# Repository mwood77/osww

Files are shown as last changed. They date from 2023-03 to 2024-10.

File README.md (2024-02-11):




<div align="center">  
  <h2>
    OSWW
    <p><i>The Open Source Watch Winder</i></p>
  </h2>
</div>

<div align="center">
  <a href="https://www.youtube.com/watch?v=BJKpY6Zp8BI" target="_blank"><strong>👉 See OSWW & Winderoo in action on youtube 👈</strong></a>
  <br>
  <br>
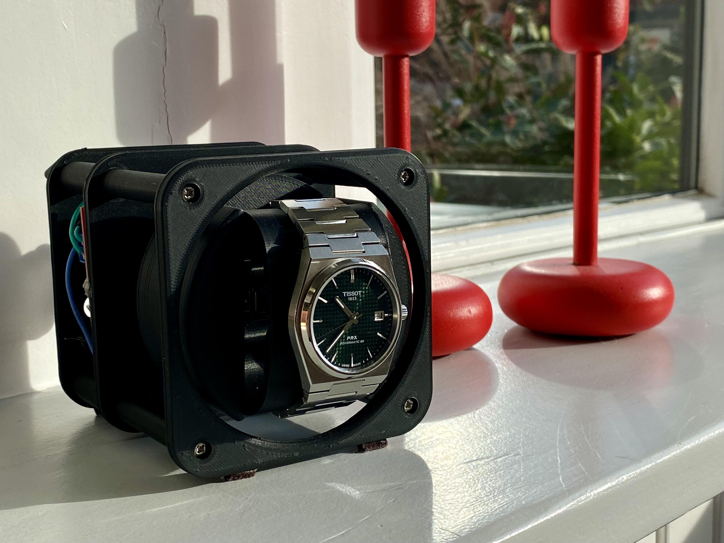
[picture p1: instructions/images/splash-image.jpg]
OSWW - The Open Source Watch Winder
  
  <br>
  <p>
    OSWW is an open source high quality, modular watch winder.
  </p>
</div>

### Key Features
* Silent belt drive
* Minimal electronics / programming experience required
* Easy to print!

## Prerequisites

### Download and install the following:
1. [Arduino IDE](https://www.arduino.cc/en/software)
1. [Add Raspberry Pi Pico to the Arduino IDE](https://www.upesy.com/blogs/tutorials/install-raspberry-pi-pico-on-arduino-ide-software)
   - Do not proceed past the heading "**Upload a program to the Pi Pico**"

## Build Instructions
1. [Bill of Materials (what you need to buy)](./instructions/bom-requirements.md)
1. [Printing Recommendations](./instructions/printing-recommendations.md)
   - [Model Files](./models)
1. [Build Guide](./instructions/build-guide.md)
1. [Wiring Diagram](./instructions/wiring-diagram.md)
1. [Upload the Code](./instructions/upload-code.md)

## Supercharge your OSWW!
> This upgrade requires a different microcontroller
- Checkout [Winderoo](https://github.com/mwood77/winderoo), which adds more complex behaviour and a GUI to your build!

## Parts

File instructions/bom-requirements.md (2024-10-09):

> [👈 Back to main page](../README.md)

# Bill of Materials & Cost

## Tools and skills you already have

- 3D printer + filament (approx 300g per winder)
- Soldering iron & the skills to use it
- Basic tools
    - Screwdriver
    - Hack saw or a rotary tool with a cut-off wheel (to cut the 4mm metal rod to size)
    - Sandpaper or files. This will depend on how dialed-in your 3D printer is.
- Epoxy glue
    - Again, whether you need this or not will depend on how dialed-in your 3D printer is.
- How to use a multimeter (we'll only check for continuity)
- Some spare small-gauge wire (ex. 22 AWG)
- Rudimentary knowledge of electronics

## Required parts
The following parts list will allow you to build:
- 1x powered winder (required)
- 2x un-powered winders (optional)

This means that you'll be able to construct a 3-watch winder. Remember that the system is modular, so if you decide to only build a single powered winder, that's ok.

### Total cost of required Parts
- **$40.00 (February 2023)**

> [!CAUTION]
> If you're planning a [Winderoo](https://github.com/mwood77/winderoo) build, do not purchase a Raspberry Pi Pico. Purchase an ESP32 instead to save some money and avoid future headaches. You can find a link to purchase an ESP32 in [Winderoo's Bill of Materials](https://github.com/mwood77/winderoo/blob/main/docs/bom-requirements.md).

| |  Quantity per Order | Link / Part Name |  Comments |  Cost Incl. Shipping |
| :-: | :---: | :---: | :---: |:-----:|
| 🔲 | 1 | [Raspberry Pi Pico](https://www.raspberrypi.com/products/raspberry-pi-pico/) | Wireless: **NO** & GPIO Headers: **NO** | $5.00 |
| 🔲 | 1 | [608ZZ bearing pack](https://nl.aliexpress.com/item/1005005321486587.html) | 10 bearings per pack | $6.00 |
| 🔲 | 1 | [Electric Motor with gear reduction](https://www.aliexpress.com/item/32987942205.html) | Select: "40 TPM" & "6V". If this is unavailable, buy a `JGA25-370` motor package with planetary gear reduction to run at 35RPM & 5V | $6.00 |
| 🔲 | 1 | [L298N Driver Board](https://nl.aliexpress.com/item/32392774289.html) | Single unit | $3.15 |
| 🔲 | 1 | [Generic Casette Belts](https://www.aliexpress.com/item/4000121675975.html) | Note - you may be able to get away with regular elastic bands, but these will long outlast elastic bands | $2.50 |
| 🔲 | 1 | [M3x20mm Screws](https://aliexpress.com/item/1005005483315023.html) | Select: "M3 50pcs" & "Length 20mm" | $4.00 |
| 🔲 | 1 | [M3 Heat Set Nuts](https://aliexpress.com/item/1005003582355741.html?) | Select: "M3(OD 5mm)" & "Length 5mm 50pcs" | $3.50 |
| 🔲 | 2 | [4mm Steel Rod](https://aliexpress.com/item/1005003594895025.html) | Select: "Diameter 4mm, length 200mm" | $3.75 |

## Optional parts
The following parts list will allow you to add:
- 1x clutch assembly
- 1x physical power button

### Total cost of optional Parts
> $10.60 (February 2023)

| |  Quantity per Order | Link / Part Name |  Comments |  Cost Incl. Shipping |
| :-: | :---: | :---: | :---: |:-----:
| 🔲  | 1 | [Steel Spring](https://aliexpress.com/item/1005002799003214.html) | Select: "25mm Length" & "Wire Diameter 0.4mm" & "Outer Diameter 10mm" | $2.60 |
| 🔲  | 1 | [Felt](https://aliexpress.com/item/1005006650225465.html) | Select: "25CMx85CM" & any colour you choose | $1.50 |
| 🔲  | 1 | [Rocker Switch](https://aliexpress.com/item/4000847897284.html) |  Select: any colour you wish & "Type1 12V LED" & "Wire Diameter 0.4mm" & "21x15mm 3Pin" | $2.10 |

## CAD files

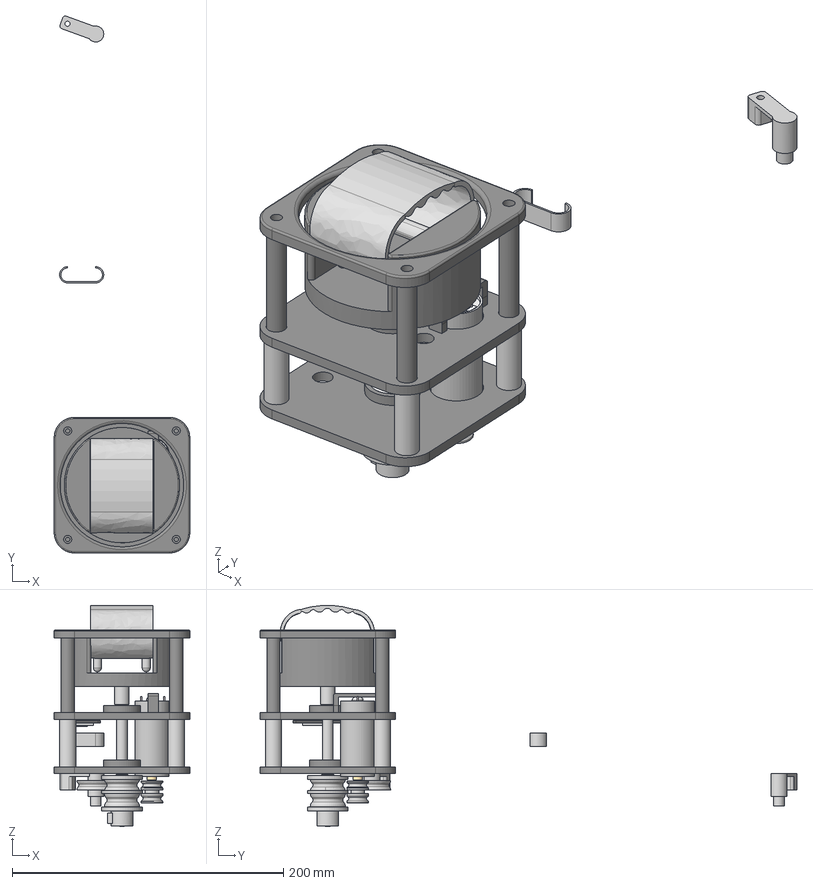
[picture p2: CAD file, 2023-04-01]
models/source-files/osww-v39-april-1-2023.step
100.0 x 395.7 x 162.9 mm
STRUCT-Back Plate-v2
STRUCT-Mid Plate-v2
STRUCT-Front Plate-v2
Brass 4mm diameter rod
Bearings x 3
Inner Race x 3
Outer Race x 3
drive dowel
brass collar
Motor Drive Pulley-v3
M4 Nylon Washer
ESP32-CPU
ESP32-PCB
ESP32-USB_PORT
Tensioner Mount_v2
Tension Pulley_v1
Horizontal Multi Clip
Watch_jig_collar-v4
Watch_Jig_driveshaft-v3
Watch_Jig-v4
Mounting_Dowel_v3 x 4
Mounting_Dowel Sleeve-v3 x 4
Watch Mount-v7
Clutchless-drive_v2
High-Mount_Drive Belt-Tensioner-v1

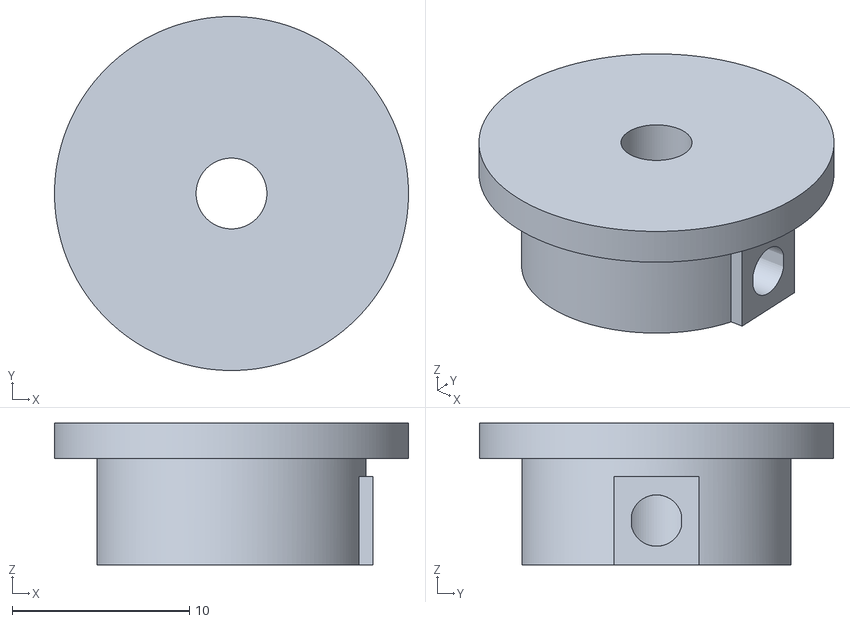
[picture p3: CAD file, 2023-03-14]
models/top_hat_v2.stl
20.0 x 20.0 x 8.00

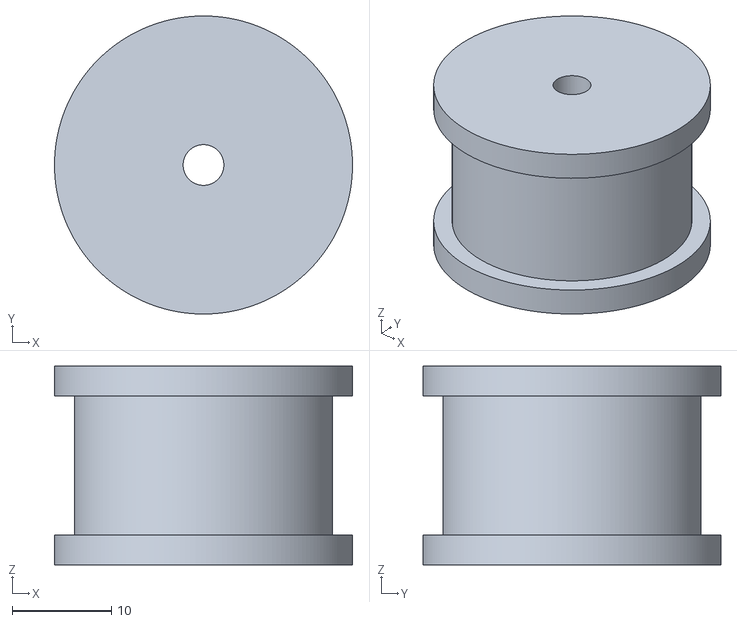
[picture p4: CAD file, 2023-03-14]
models/spring_holder_v3.stl
30.0 x 30.0 x 20.0

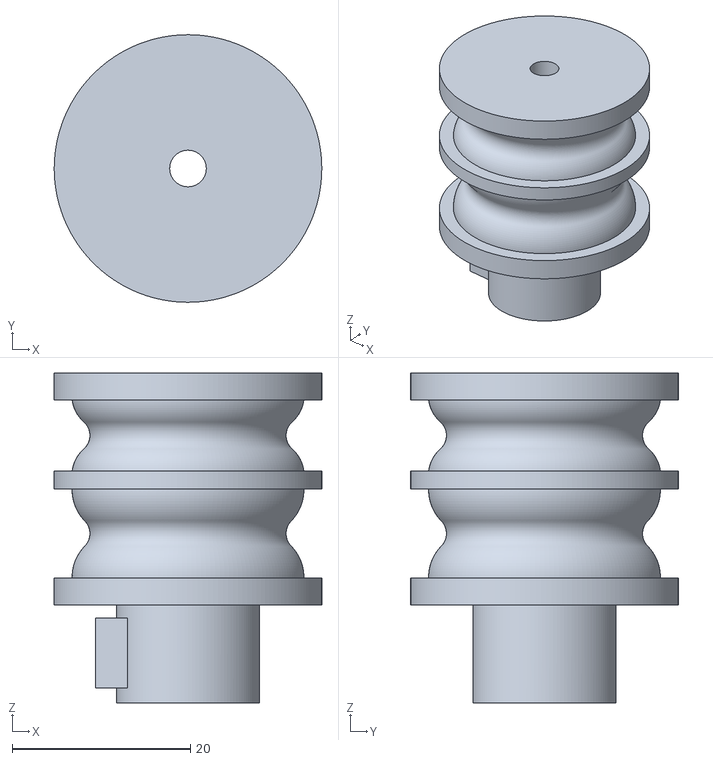
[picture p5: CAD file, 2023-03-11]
models/clutchless_drive_pulley_v2.stl
30.0 x 30.0 x 37.0

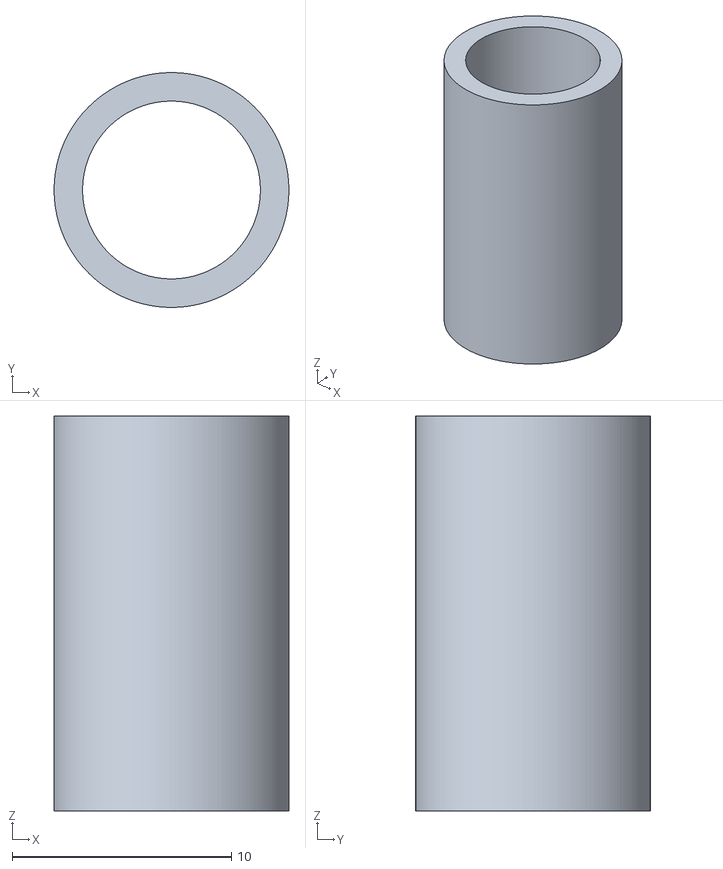
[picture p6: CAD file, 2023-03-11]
models/watch_jig_collar_v4.stl
10.7 x 10.7 x 18.0

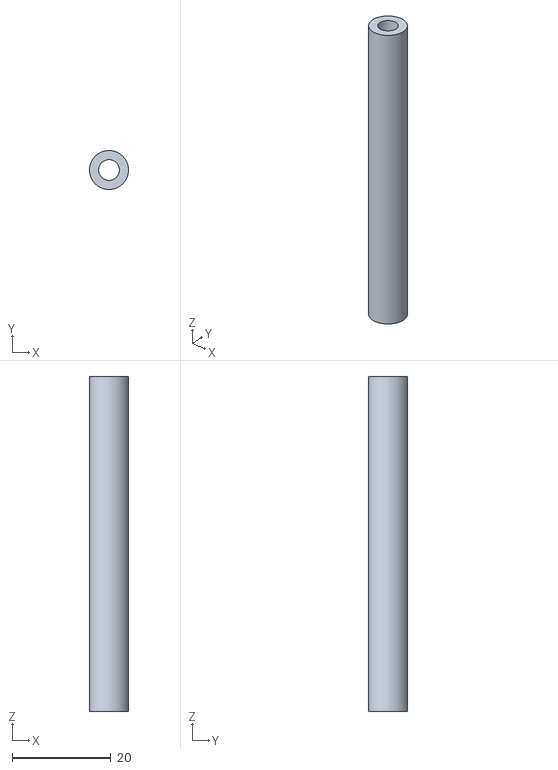
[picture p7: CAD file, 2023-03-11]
models/watch_jig_driveshaft_v3.stl
7.92 x 7.92 x 68.0

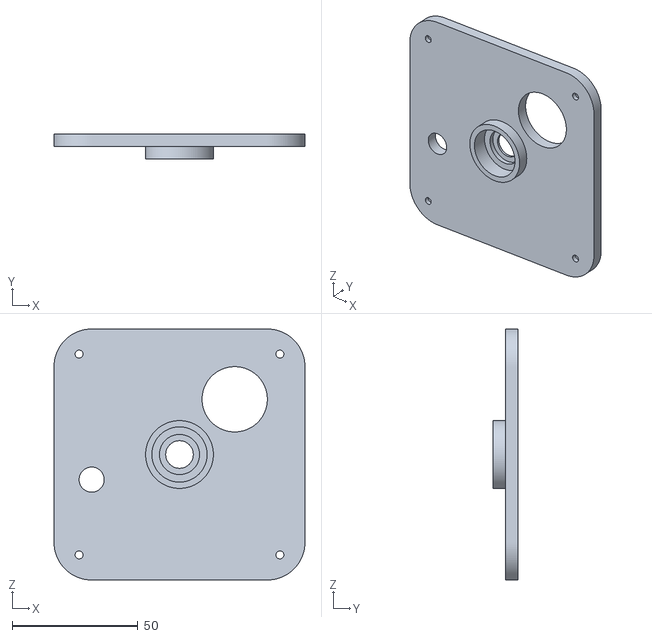
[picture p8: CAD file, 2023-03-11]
models/STRUCT_back_plate_v2.stl
100.0 x 10.0 x 100.0

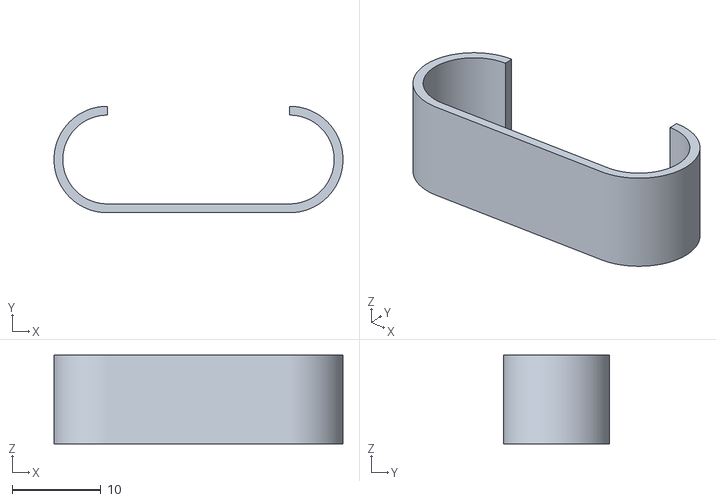
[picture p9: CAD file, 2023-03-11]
models/multi_clip.stl
32.6 x 12.0 x 10.0

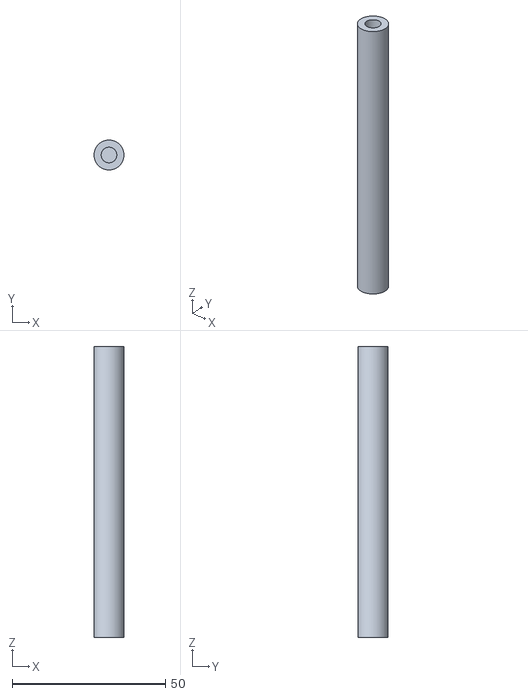
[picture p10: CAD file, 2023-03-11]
models/mounting_dowel_v3.stl
9.80 x 9.80 x 95.0

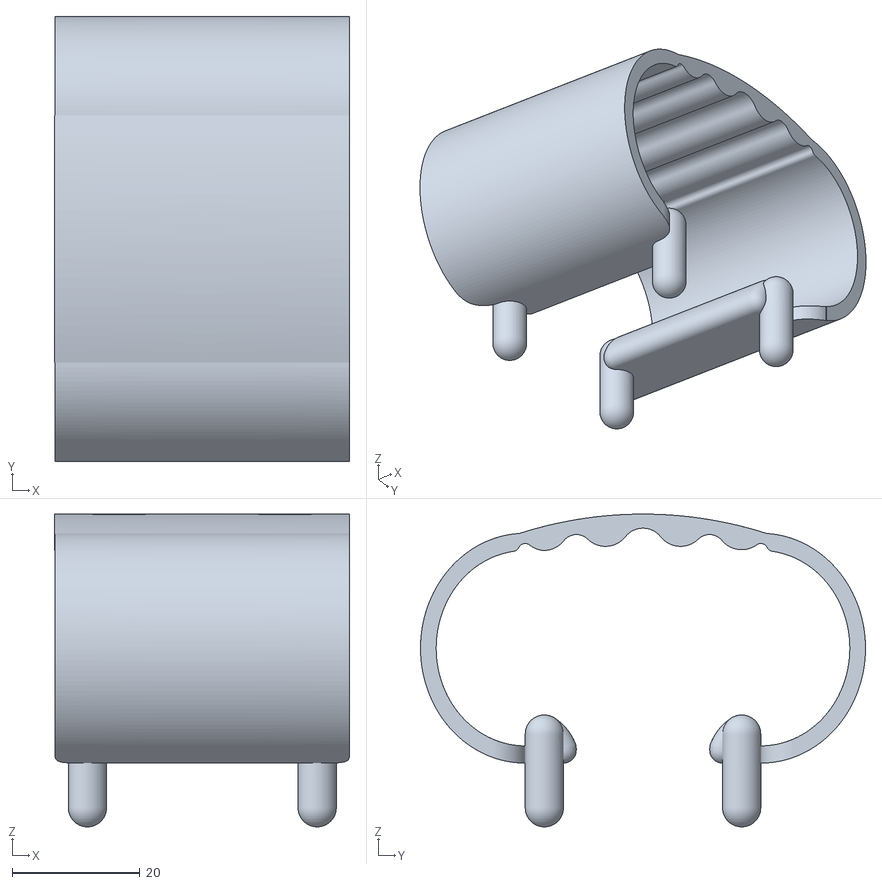
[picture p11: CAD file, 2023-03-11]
models/watch_mount_v7.stl
46.3 x 69.7 x 49.0

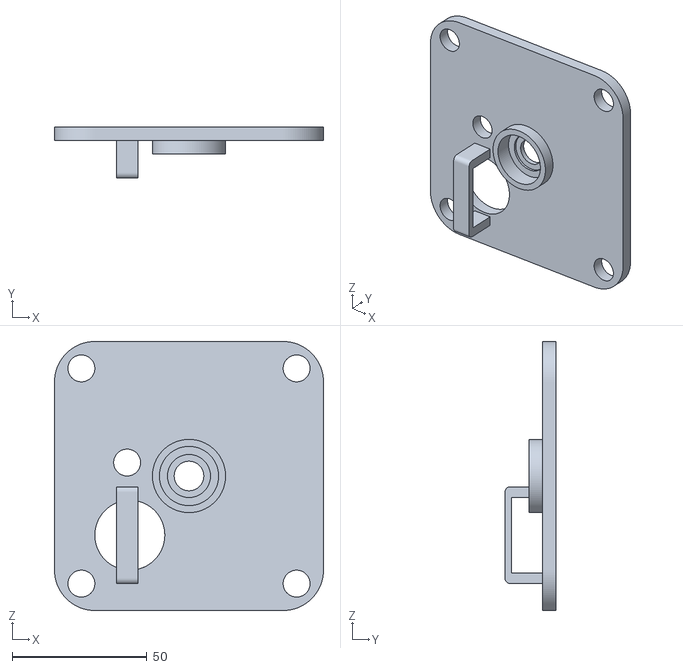
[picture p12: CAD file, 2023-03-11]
models/STRUCT_mid_plate_v2.stl
100.0 x 19.0 x 100.0

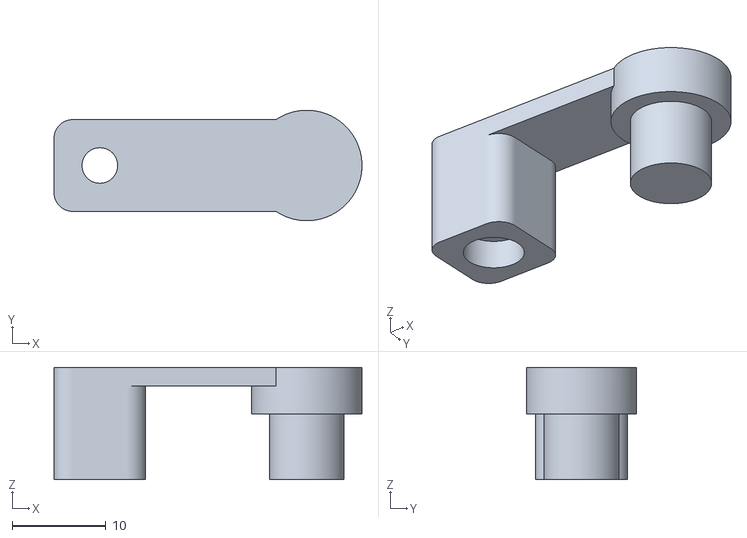
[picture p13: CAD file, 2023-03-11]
models/tensioner_pulley_mount_v2.stl
32.9 x 11.8 x 12.0

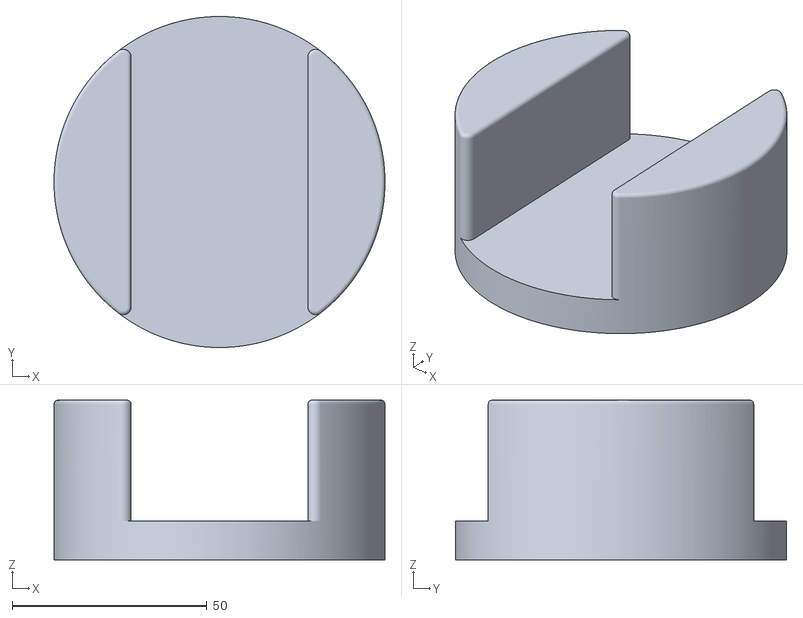
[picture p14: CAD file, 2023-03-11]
models/watch_jig_v4.stl
85.0 x 85.0 x 41.0

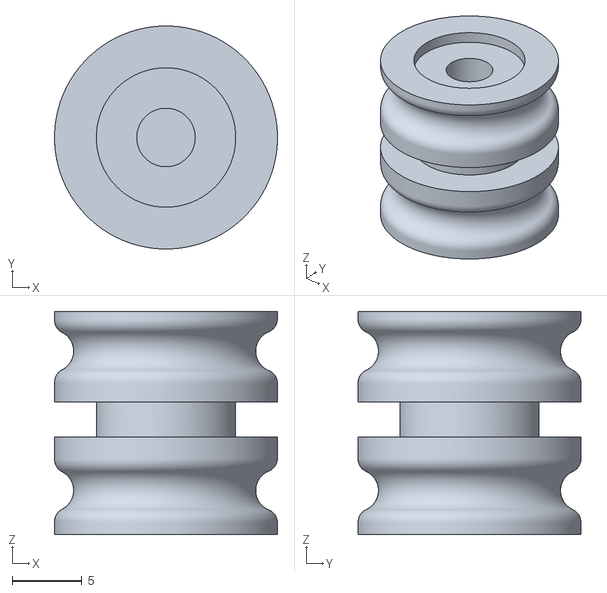
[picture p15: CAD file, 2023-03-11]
models/motor_drive_pulley_v3.stl
16.0 x 16.0 x 16.0

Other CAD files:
models/STRUCT_front_plate_v2.stl
models/high_position_tensioner_pulley_mount_v1.stl
models/tensioner_pulley_v1.stl
models/mounting_dowel_sleeve_v3.stl
models/source-files/osww-v39-april-1-2023.f3d

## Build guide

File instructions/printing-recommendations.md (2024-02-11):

> [👈 Back to main page](../README.md)

# Printing Recommendations
> [!NOTE]
> Total time spent printing is 24 hours per winding unit
>
> Total filament used is approximately 300g per winder

* These are general priting recommendations. 
* Remember that you know your printer better than I.

## General Advice
1. The following models will require support:
    * `STRUCT_mid_plate`
    * `watch_mount`
1. The model is designed to be printed with PLA, therefore tolerances are spec'd for that
    * Tolerances are between `0.1 - 0.2mm`
1. Print with 25% infill
    * This will the increase overall rigidity of the model, especially when dealing with the motor's torque.
    * This will also give you a "premium feeling" product.
1. [If your printer has a tendency elephant foot](https://3dprinterly.com/how-to-fix-bottom-of-3d-print-that-looks-bad/), you'll need to file down some of the pieces.
    * For example, the `mounting_dowel`'s outter lip will need to be filed down so the `mounting_dowel_sleeve` can easily slip over it.

## Recommended Printing Orientation and Print Duration by Model

| Model Name | Quantity To Print | Printing Time Per Unit | Printing Orientation |
| :---: | :---: | :---: | :---:|
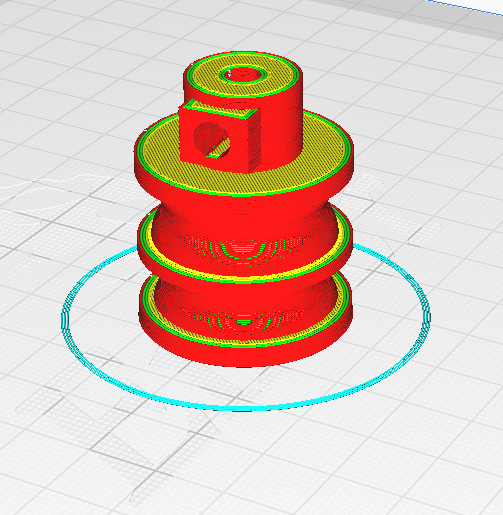
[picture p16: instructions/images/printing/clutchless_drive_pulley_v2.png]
drive_pulley
| `clutchless_drive_pulley_v2` | 1 | 2 hours |  |
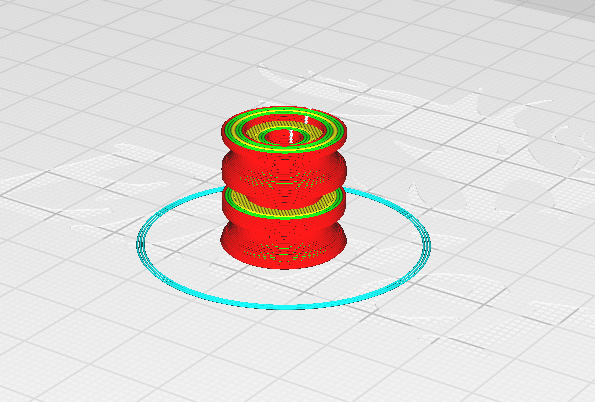
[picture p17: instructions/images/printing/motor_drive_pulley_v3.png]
motor_drive_pulley
| `motor_drive_pulley_v3` | 1 | 0.5 hours |  |
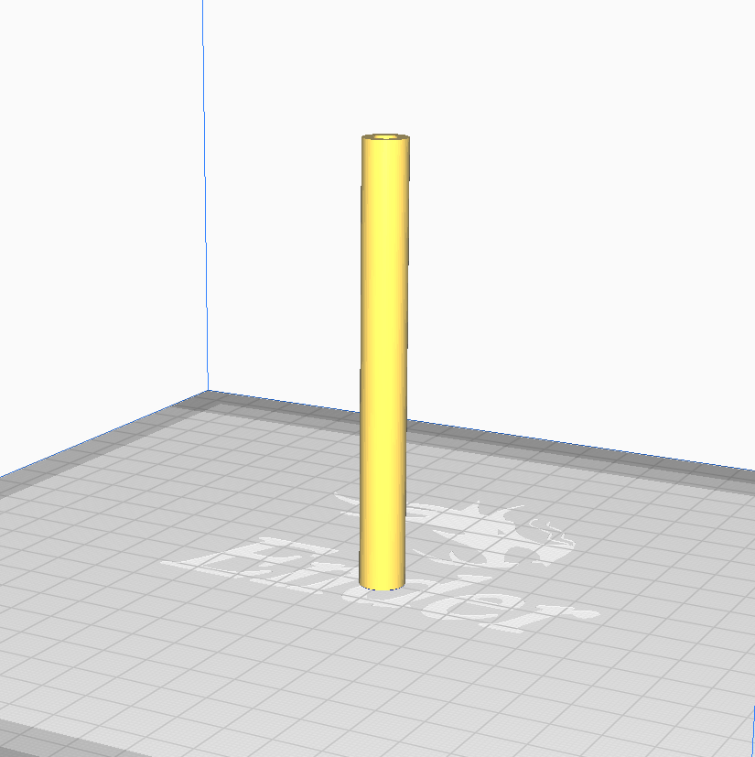
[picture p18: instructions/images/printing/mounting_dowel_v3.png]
mounting_dowel
| `mounting_dowel_v3` | 4 | 0.75 hours p/unit |  |
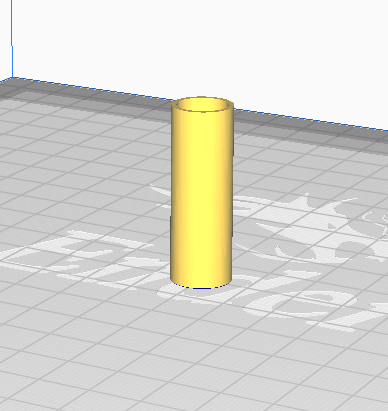
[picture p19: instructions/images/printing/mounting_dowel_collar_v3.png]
mounting_dowel_sleeve
| `mounting_dowel_sleeve_v3` | 4 | 0.25 hours p/unit |  |
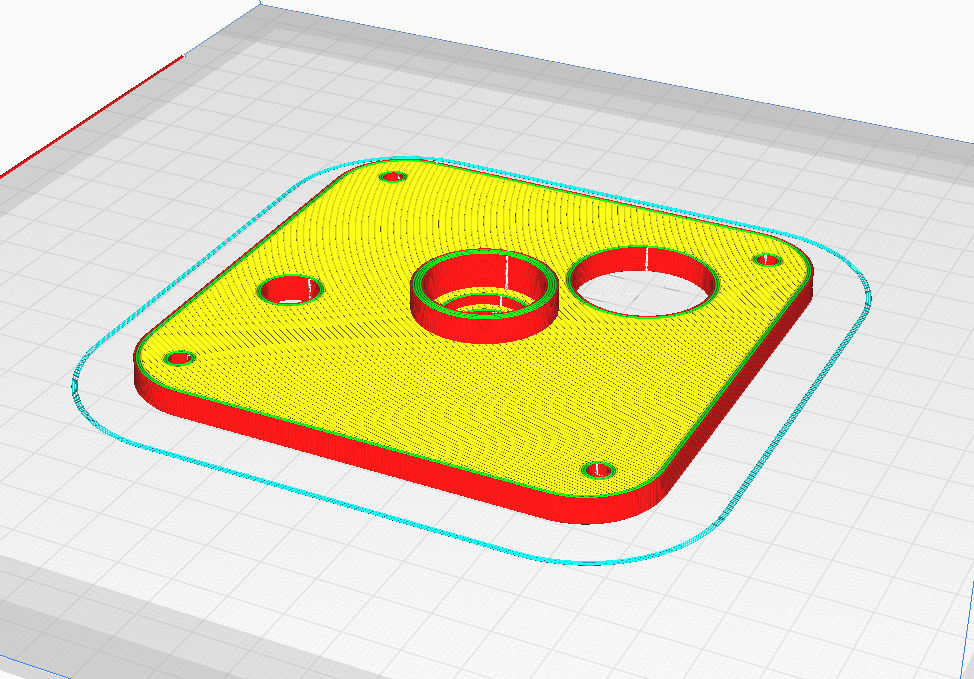
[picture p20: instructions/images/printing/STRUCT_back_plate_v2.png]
STRUCT_back_plate
| `STRUCT_back_plate_v2` | 1 | 3 hours |  |
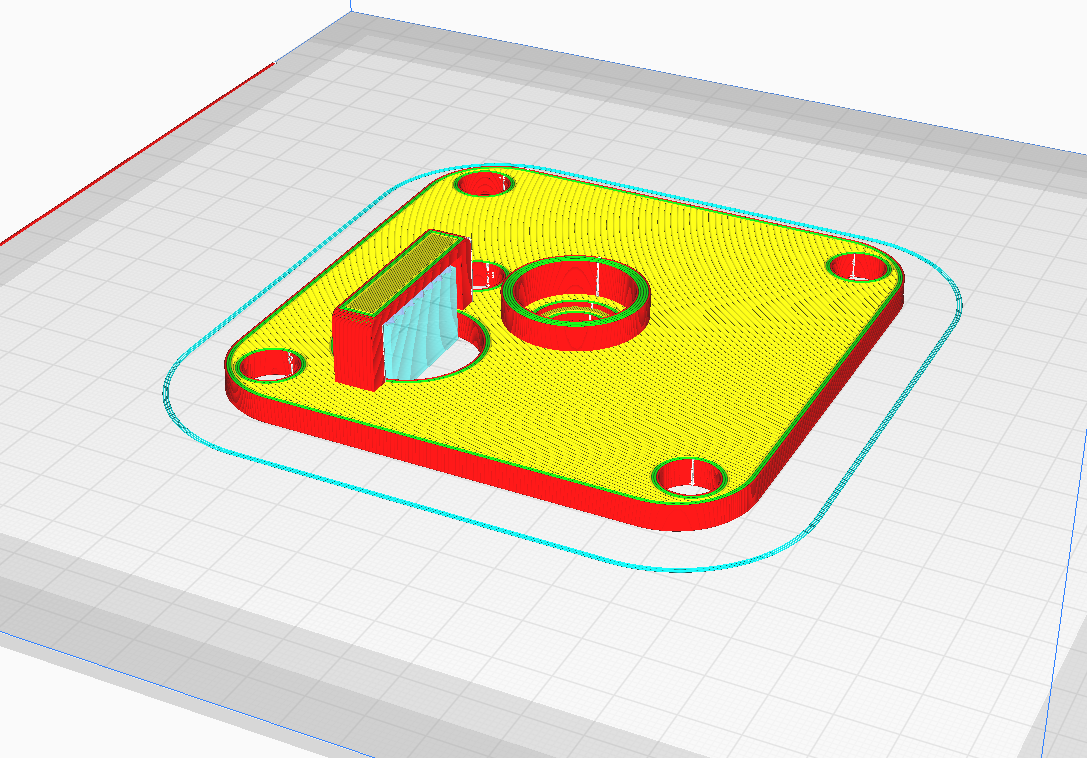
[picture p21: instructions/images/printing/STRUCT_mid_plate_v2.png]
STRUCT_mid_plate
| `STRUCT_mid_plate_v2` | 1 | 3 hours |  |
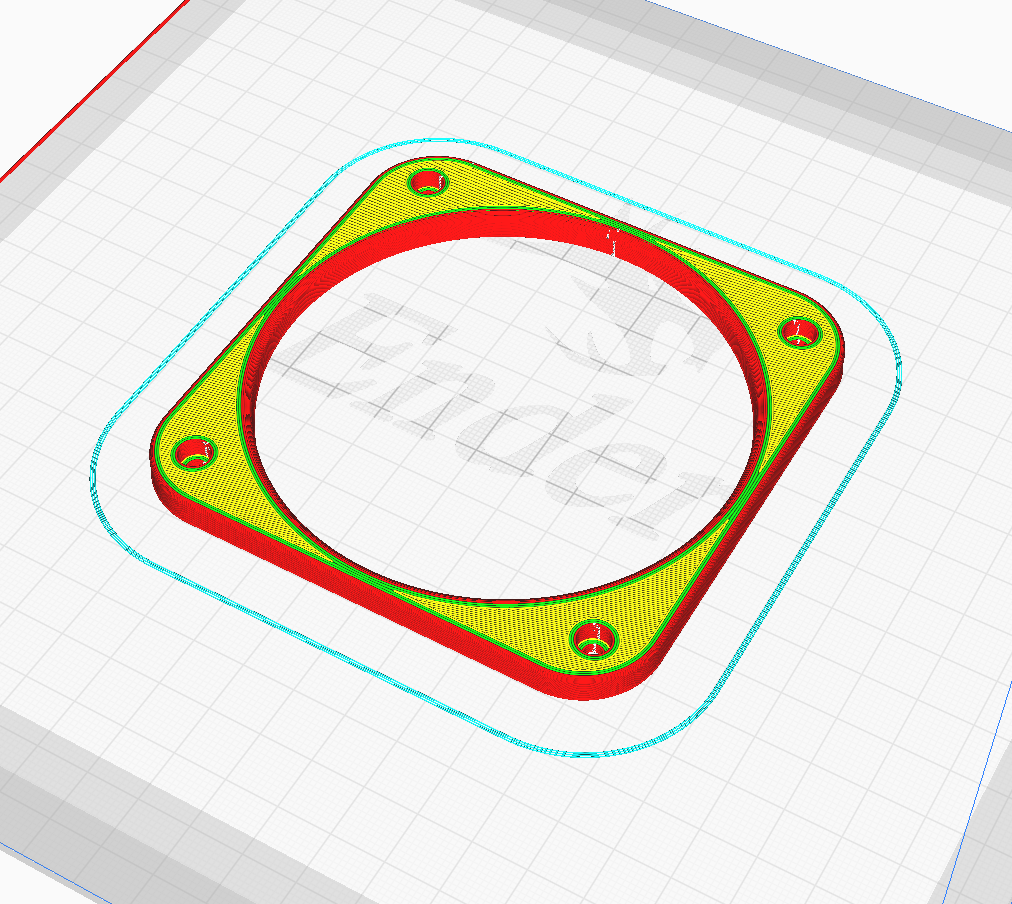
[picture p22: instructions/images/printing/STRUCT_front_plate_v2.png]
STRUCT_front_plate
| `STRUCT_front_plate_v2` | 1 | 2 hours |  |
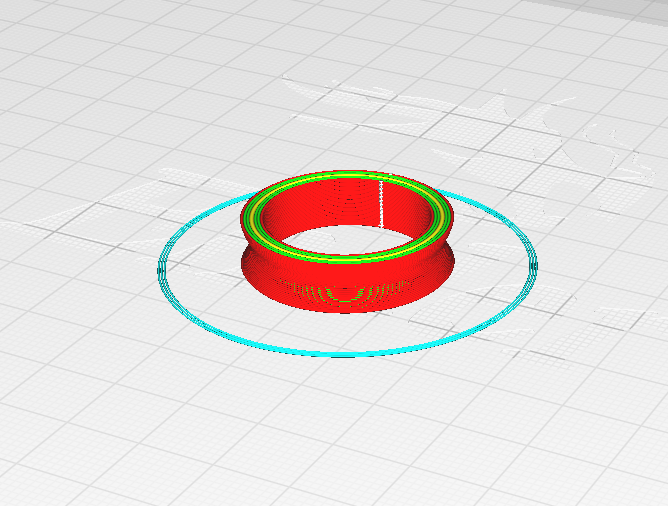
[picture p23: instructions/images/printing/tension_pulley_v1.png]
tensioner_pulley_mount
| `tensioner_pulley_v1` | 1 | 0.25 hours |  |
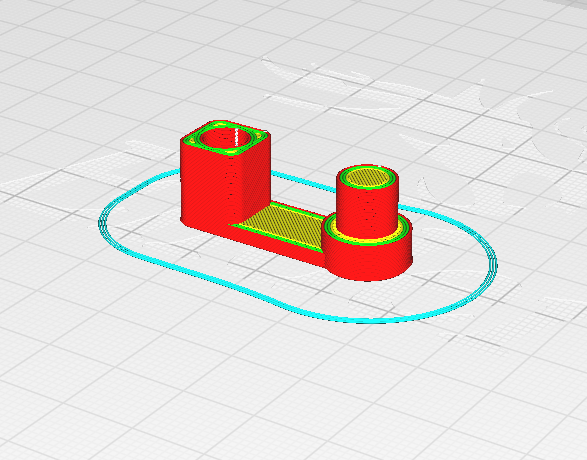
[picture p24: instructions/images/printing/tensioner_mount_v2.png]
tensioner_mount
| `tensioner_pulley_mount_v2` | 1 | 0.25 hours |  |
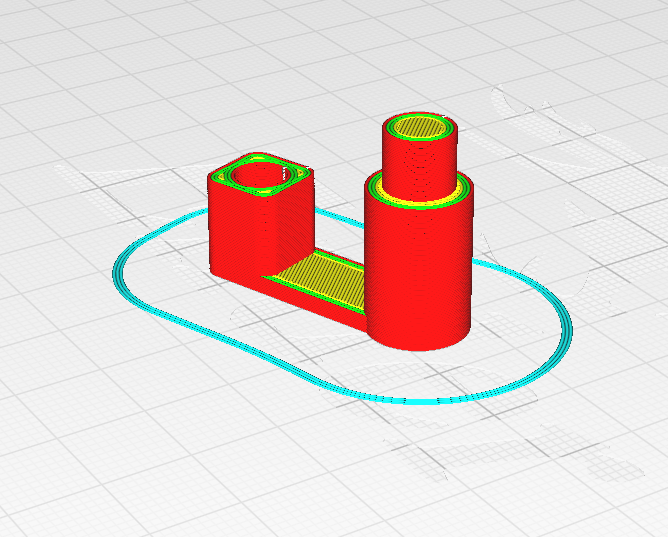
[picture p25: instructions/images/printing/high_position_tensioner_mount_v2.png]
high_position_tensioner_mount
| `high_position_tensioner_pulley_mount_v1` | 1 | 0.25 hours |  |
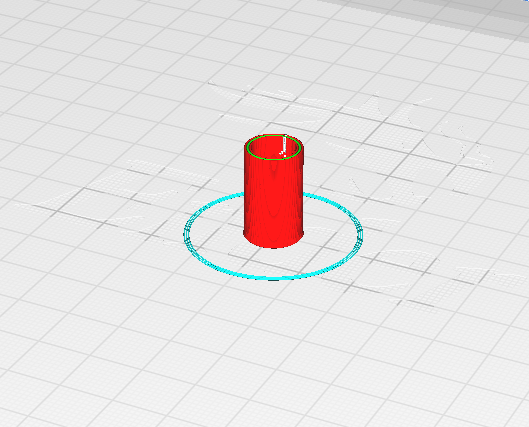
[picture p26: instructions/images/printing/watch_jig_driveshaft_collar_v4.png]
watch_jig_collar
| `watch_jig_collar_v4` | 1 | 0.25 hours |  |
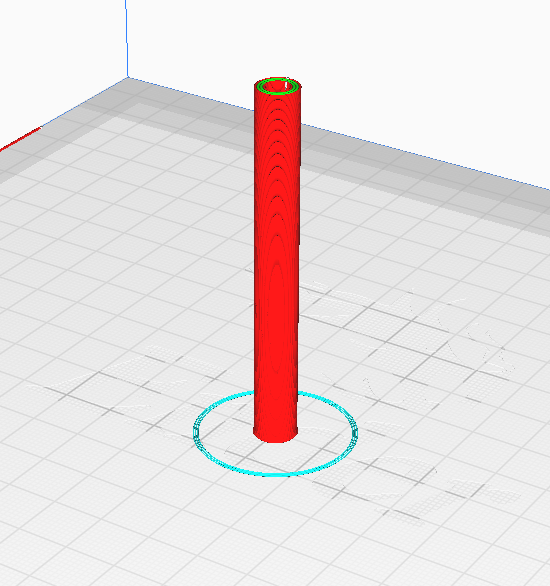
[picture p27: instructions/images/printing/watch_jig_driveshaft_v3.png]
watch_jig_driveshaft
| `watch_jig_driveshaft_v3` | 1 | 1 hour |  |
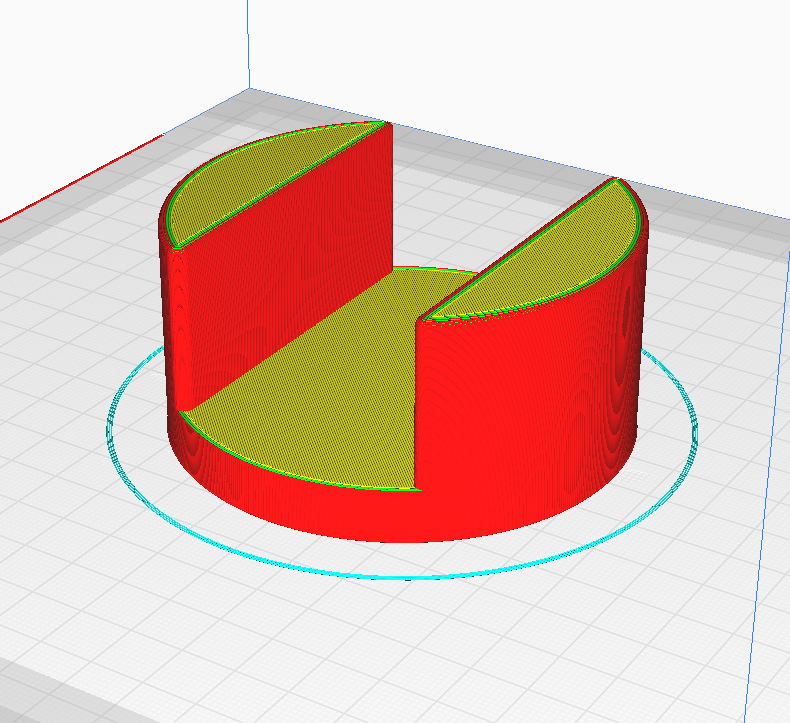
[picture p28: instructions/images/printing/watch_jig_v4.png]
watch_jig
| `watch_jig_v4` | 1 | 6 hours |  |
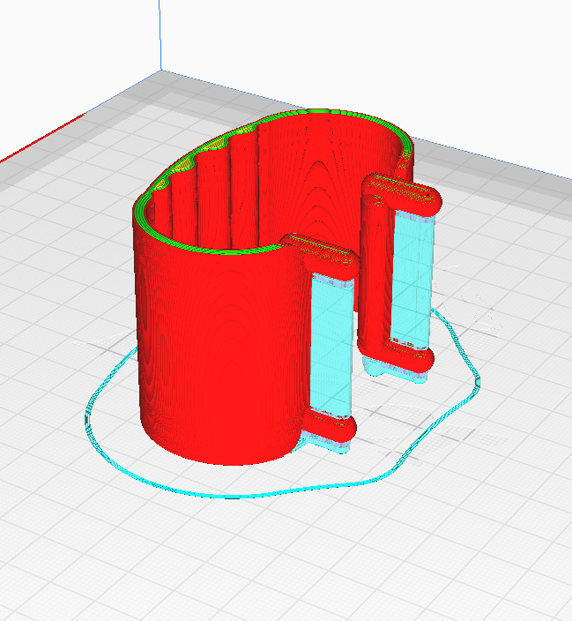
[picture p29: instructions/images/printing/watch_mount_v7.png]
watch_mount
| `watch_mount_v7` | 1 | 2 hours |  |
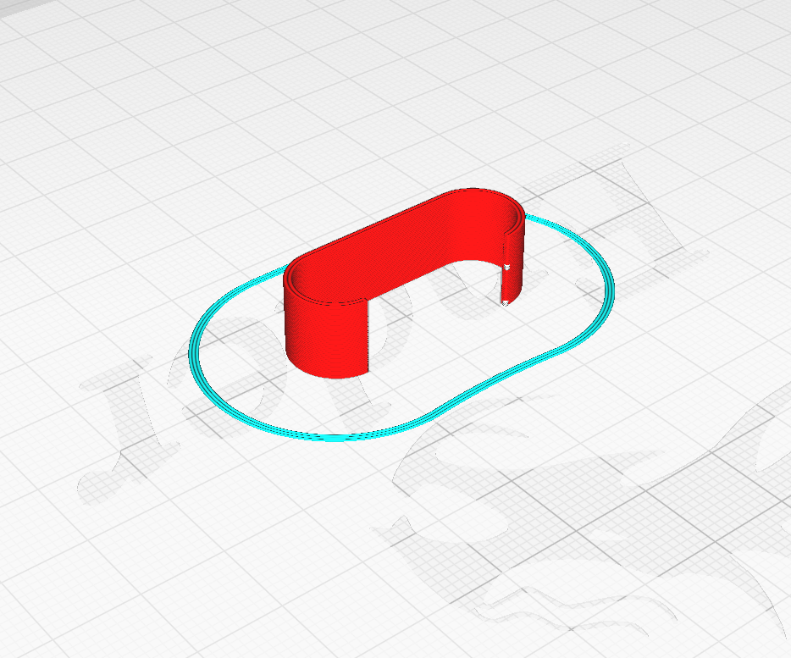
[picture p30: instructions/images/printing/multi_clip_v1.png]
multi_clip
| `multi_clip` | 4 | 0.25 hours p/unit |  |
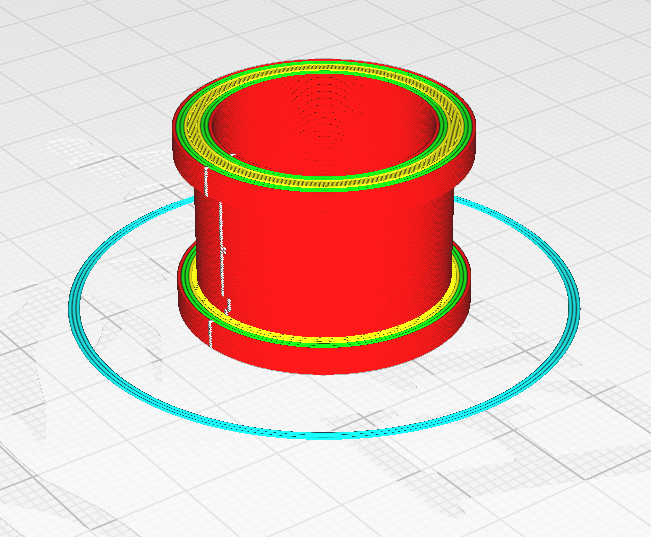
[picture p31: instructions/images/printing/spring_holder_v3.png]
spring_holder_v3
| `spring_holder_v3` | 1 | 1 hours |  |
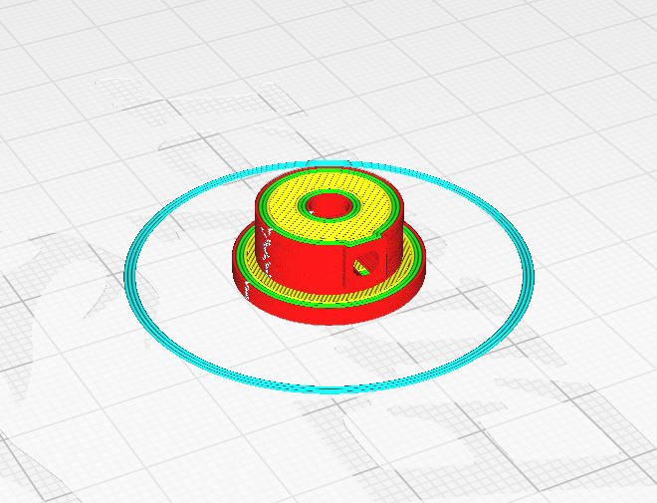
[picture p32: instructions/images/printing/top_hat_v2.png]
top_hat_v2
| `top_hat_v2` | 1 | 0.25 hours |  |

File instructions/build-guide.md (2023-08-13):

> [👈 Back to main page](../README.md)

# Building your Winder

> *Make sure you've ordered all required materials first!*
> - [You can find the ***Bill of Materials*** here](./bom-requirements.md)

 ## Assembly legend and definitions
 - Text formatted `like_this` referes to a 3D printed model, by filename
 - Text formatted ***like this*** (bold & italicized) referes to a purchased part from the Bill of Materials
 - Bore - the long cylindrical hollow part of something. [^1]
 - Flush - smoothly aligned, not sticking out. [^2]

## Watch Jig Assembly

> :warning: This assembly may require epoxy glue and sandpaper/filing. The driveshaft assembly is a tight, friction fit, and must be centered inside the jig’s bore.

### Required parts:
- ***4mm rod***
- `watch_jig` model
- `watch_jig_collar` model
- `watch_jig_driveshaft` model

### Steps:
1. Cut the ***4mm rod*** to 110mm in length, then de-burr the ends with a file or sandpaper.
1. Test fit the `watch_jig` and `watch_jig_collar`. They should begin to push together by hand. If your printer is dialed in, these two parts will be a tight friction fit. Flip the assembly upside down and rest the collar against a flat surface. Place your thumbs overtop of the center of the `watch_jig` and push down. The `watch_jig_collar` should drive itself into the `watch_jig`’s body. 
    - If the `watch_jig` and `watch_jig_collar` don’t fit together, lightly sand/file the lip of the `watch_jig_collar` until it fits inside the `watch_jig`’s bore.
    <div align="center">
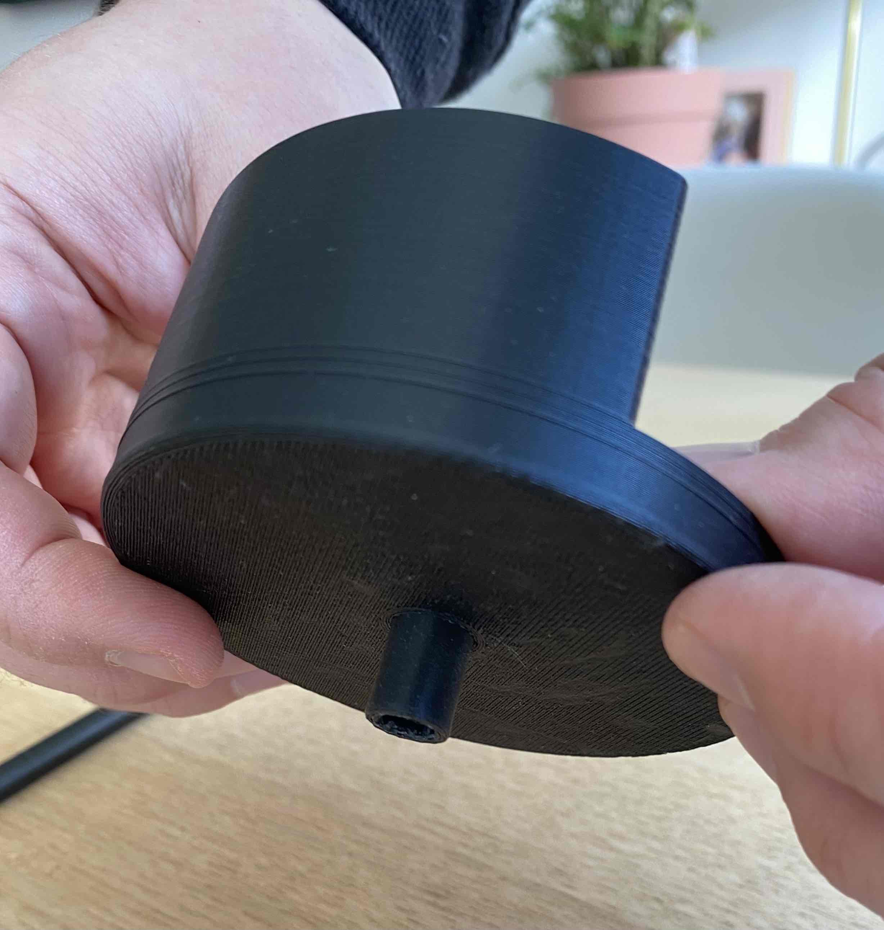
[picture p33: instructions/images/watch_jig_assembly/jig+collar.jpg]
jig with collar loosely fit
          
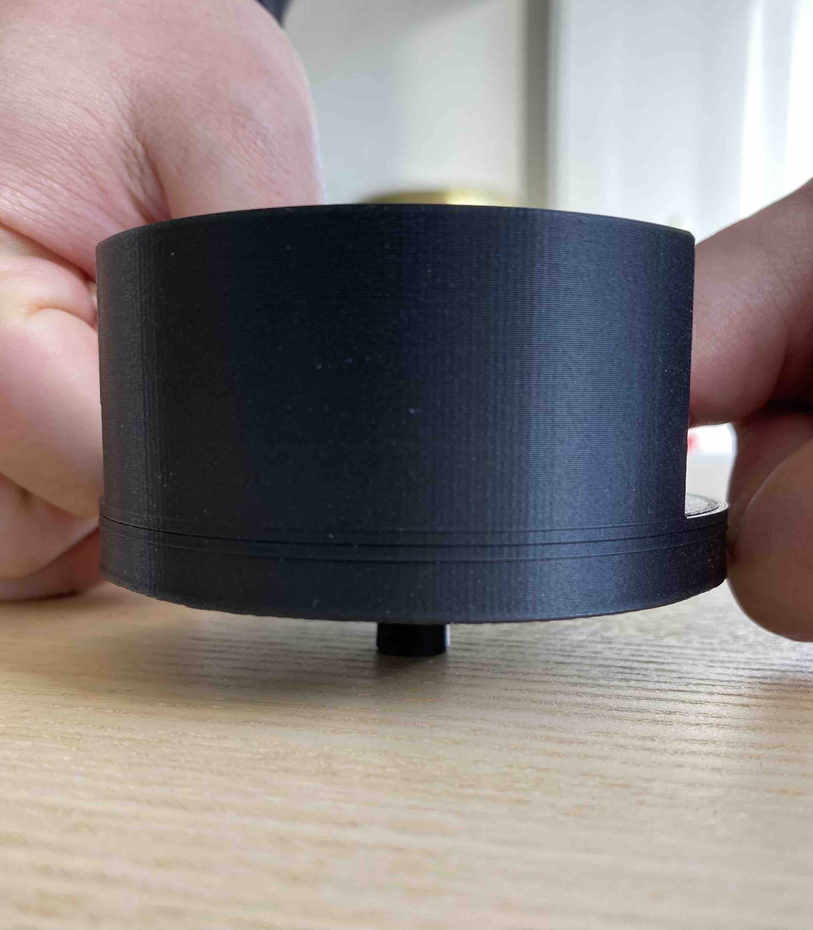
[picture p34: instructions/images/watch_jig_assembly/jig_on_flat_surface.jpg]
jig resting on flat surface
         
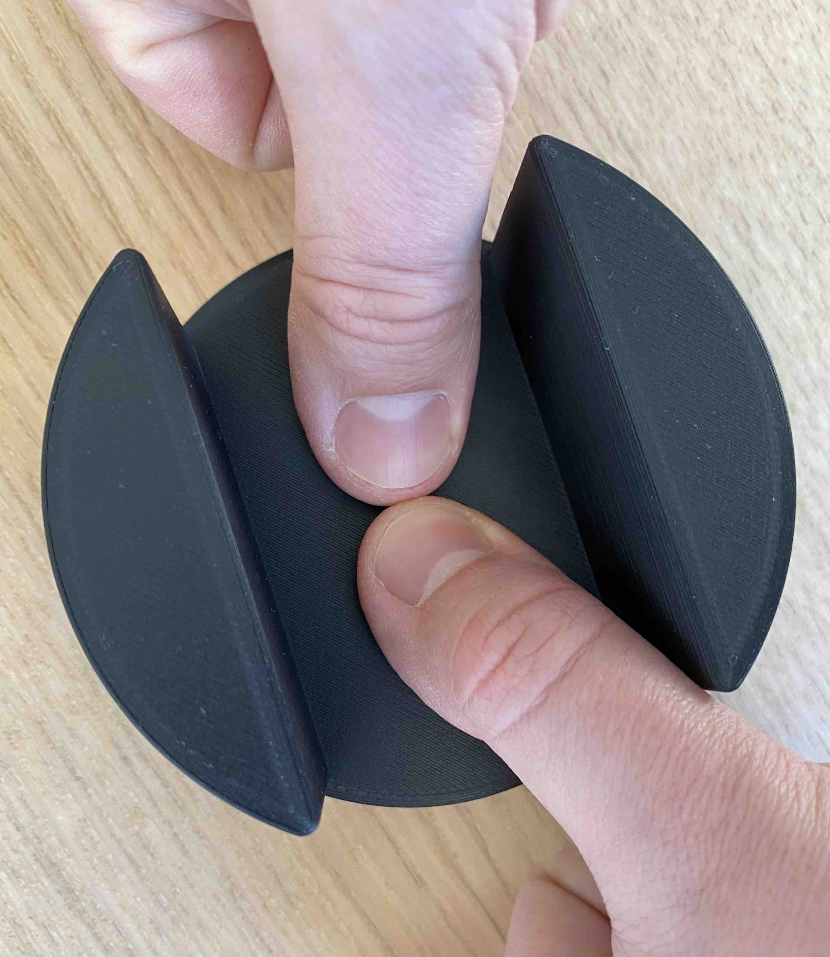
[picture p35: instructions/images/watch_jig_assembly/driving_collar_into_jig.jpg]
driving the collar into jig's bore
         
    <div>
1. Test fit the ***4mm rod*** and `watch_jig_driveshaft` model. Again this will be a tight fit, but the rod should be able to move through the `watch_jig_driveshaft`’s bore with a twisting motion; hold the `watch_jig_driveshaft` and twist/push the metal rod through the bore. If this isn’t possible, file the `watch_jig_driveshaft`’s inner bore to fit.
    <div align="center">
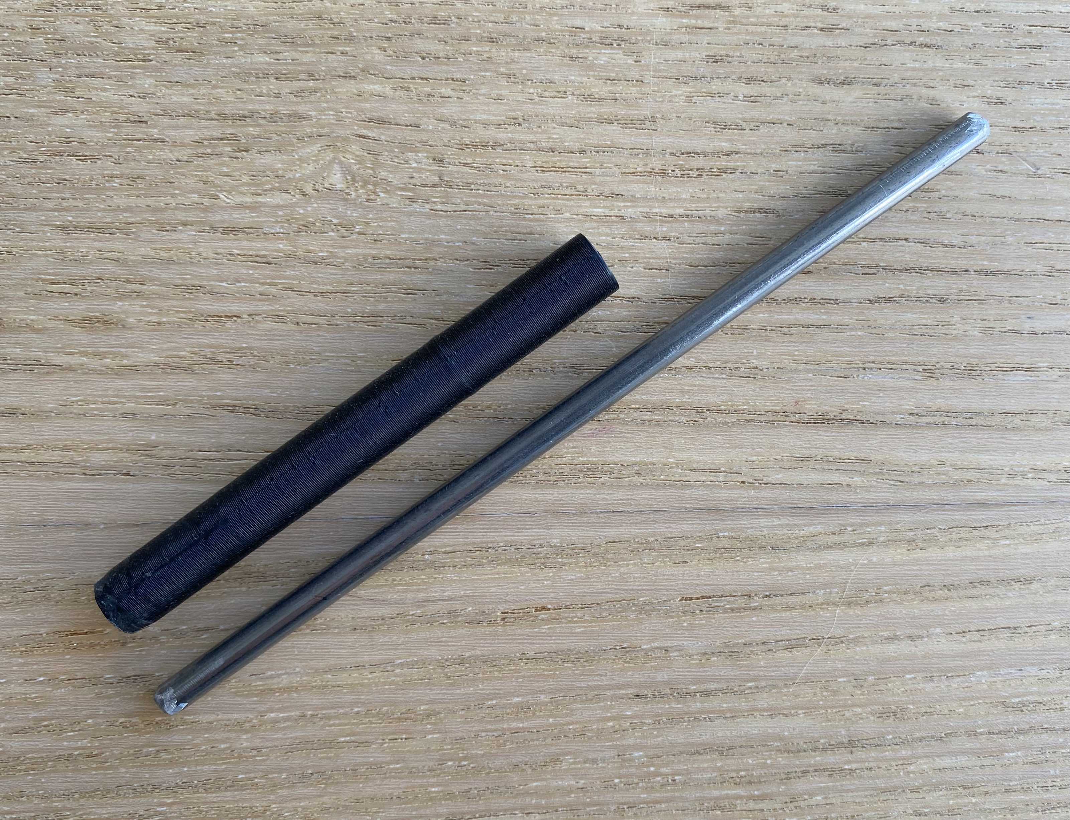
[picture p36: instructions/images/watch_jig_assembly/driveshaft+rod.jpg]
4mm rod + driveshaft
          
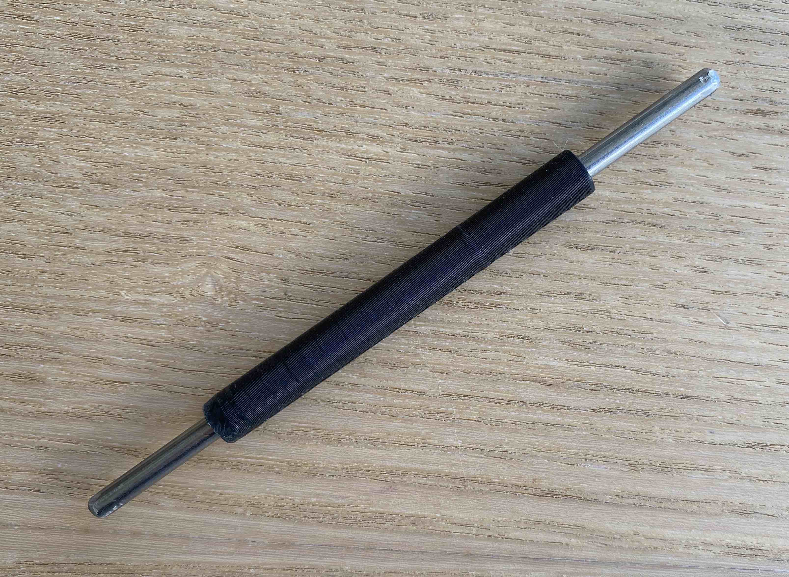
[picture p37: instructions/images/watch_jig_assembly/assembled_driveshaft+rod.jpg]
assembled rod + driveshaft
         
    <div>
1. **Read the next step in full before you begin!** 
1. Do a partial test fit  of the driveshaft/rod assembly and the jig/collar assembly. The driveshaft assembly should start to drive into the collar's bore with the same twist/push motion you used to drive the metal rod through the driveshaft. **DO NOT FULLY SEAT THE ASSEMBLIES YET**. Now do the following:
    - Remove the driveshaft assembly from the jig assembly again
    - Move the `watch_jig_driveshaft` to halfway down the ***4mm Rod***, like so
        <div align="center">assembled rod + driveshaft</div>
    - Apply a drop of ***epoxy glue*** inside the `watch_jig_collar`'s bore with something small (ex. toothpick). Make sure the epoxy is at the bottom.
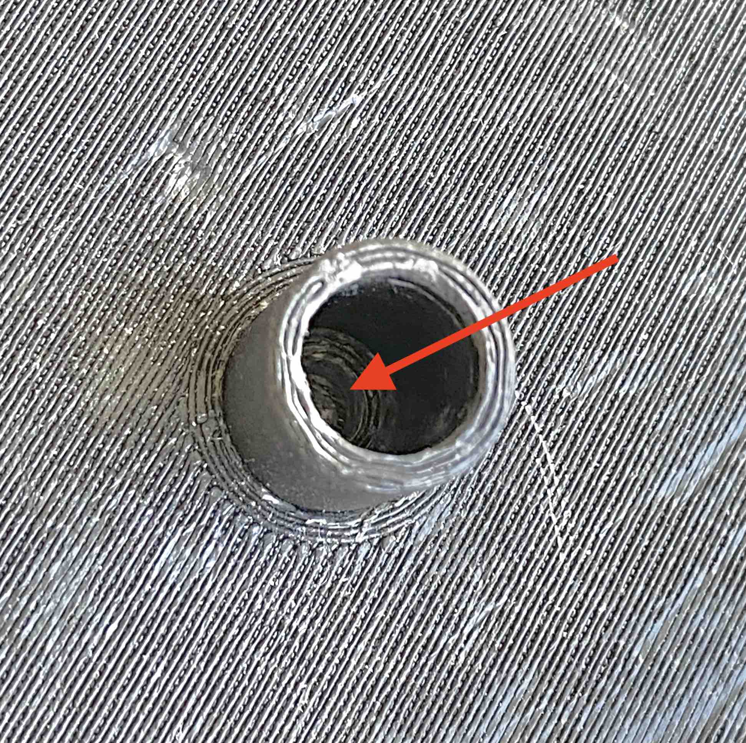
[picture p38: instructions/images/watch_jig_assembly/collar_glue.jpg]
where to glue in collar
        
    - Take the driveshaft and jig assemblies in your hands; align the metal rod in the center of the `watch_jig_collar`'s bore. This should self-center. Place the jig assembly upside down on a flat surface and *gently* push the `watch_jig_driveshaft` down the bore until it fully seats. Pick up the complete assembly and verify that the driveshaft is vertically aligned and the assembly rotates true. Leave the assembly upside down (driveshaft points to the sky) and allow the epoxy to dry.
        <div align="center">final assembly gif</div>

## Tensioner Assembly / High Position Tensioner Assembly

### Required parts:
- 1x ***608ZZ bearing***
- `tensioner_pulley` model
- `tensioner_pulley_mount` model

> :warning: This assembly may require epoxy glue and sandpaper/filing. The outter pulley and inner pulley mount should be a tight friction fit. However, not all 608ZZ bearings are made equal and may require a touch of glue to secure the models to the bearing.

### Steps:
1. Test fit the `tensioner_pulley` and ***608ZZ bearing***; these should should press-fit together. If they do not, lightly sand/file the inner bore of the `tensioner_pulley` until it begins to fit over the bearing. Drive the pulley down the bearing until the bearing and pulley faces are flush.
    <div align="center">
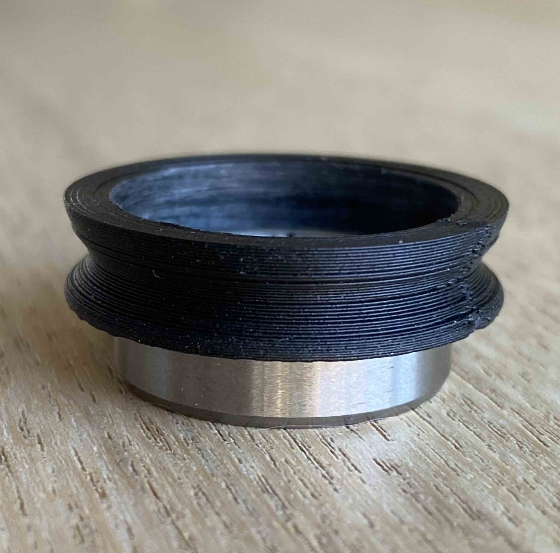
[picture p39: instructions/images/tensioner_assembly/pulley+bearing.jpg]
tensioner pulley partial fit over 608ZZ bearing
          
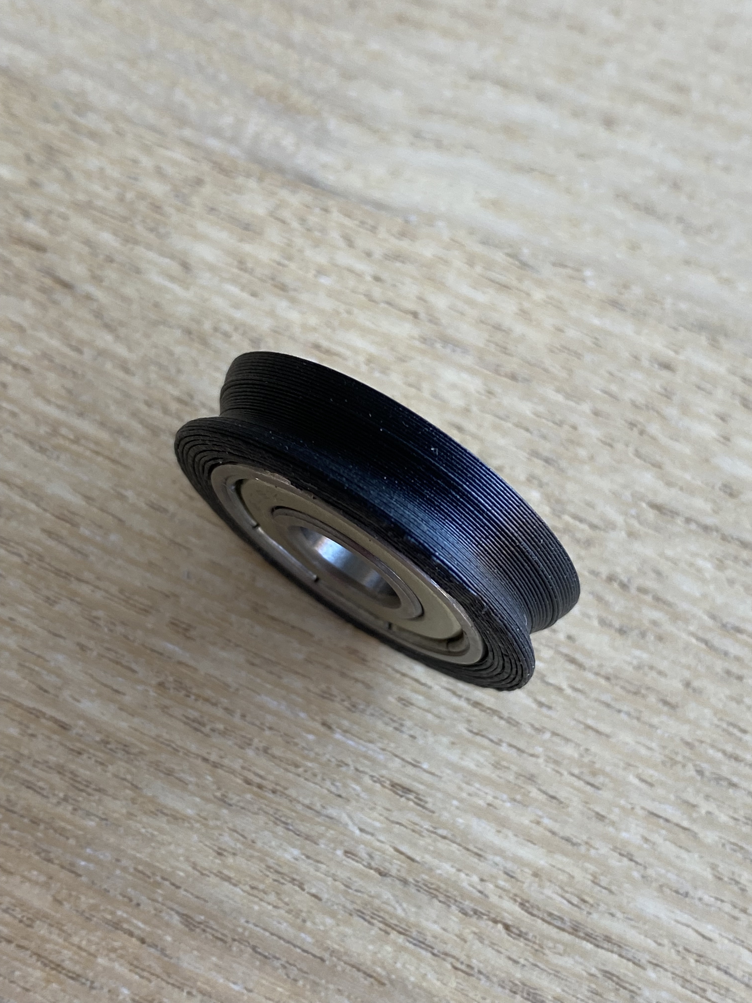
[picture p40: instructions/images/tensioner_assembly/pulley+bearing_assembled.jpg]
tensioner pulley and bearing flushed
          
    <div>
1. Test fit the bearing's center race overtop of the `tensioner_pulley_mount`; these should should press-fit together. If they do not, lightly sand/file the mounting peg of the `tensioner_pulley_mount` until the bearing begins to fit. Drive the bearing down the tensioner's mounting peg until the bearing and peg's faces are flush.
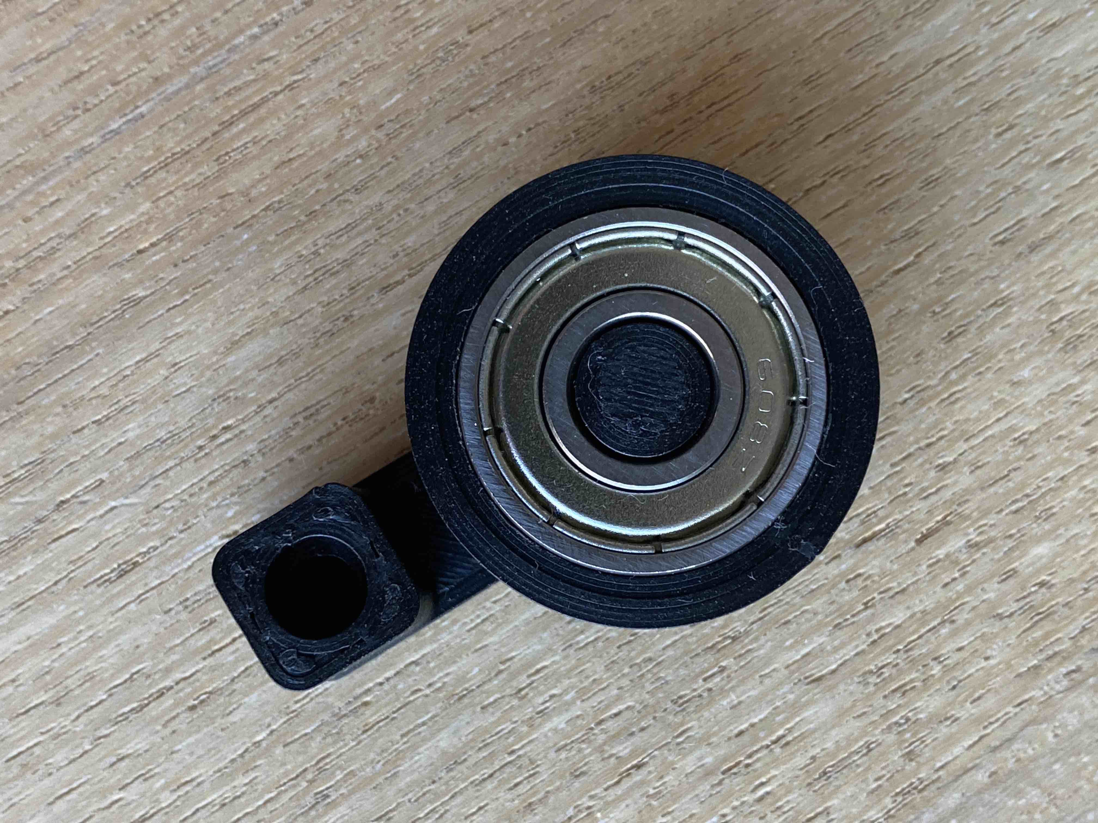
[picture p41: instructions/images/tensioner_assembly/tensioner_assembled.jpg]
tensioner assembled
    <div align="center"><div>
1. The bearing's **center** should not be loose or rotate around the mounting peg. If it does, apply a small drip of epoxy to the peg's base. If you find it difficult to tell, hold the tensioner mount in one hand and rotate the pulley. If you can feel any kind of vibration, you need to apply glue. If the bearing is a tight fit, you should feel no vibration.

## Mounting Dowel Assembly

> :warning: You must create 4 of these assemblies

> :warning: This assembly may require sandpaper/filing. The fitment between the `mounting_dowel` and `mounting_dowel_sleeve` is a tight friction fit.

### Required parts per assembly:
- 2x ***M3 Heat Set Nuts***
- `mounting_dowel` model
- `mounting_dowel_sleeve` model

1. Setup your soldering iron. We'll need it to insert our heat set nuts into each dowel end.
1. While your soldering iron is heating up, test fit the `mounting_dowel` and `mounting_dowel_sleeve`. They should begin to push together by hand. If your printer is dialed in, these two parts will be a tight friction fit. Flip the assembly upside down so that the open end of the `mounting_dowel_sleeve` is resting on a flat surface. Gently push down on the `mounting_dowel` until it slides into place and the face of the dowel and sleeve are flush.

    <div align="center">
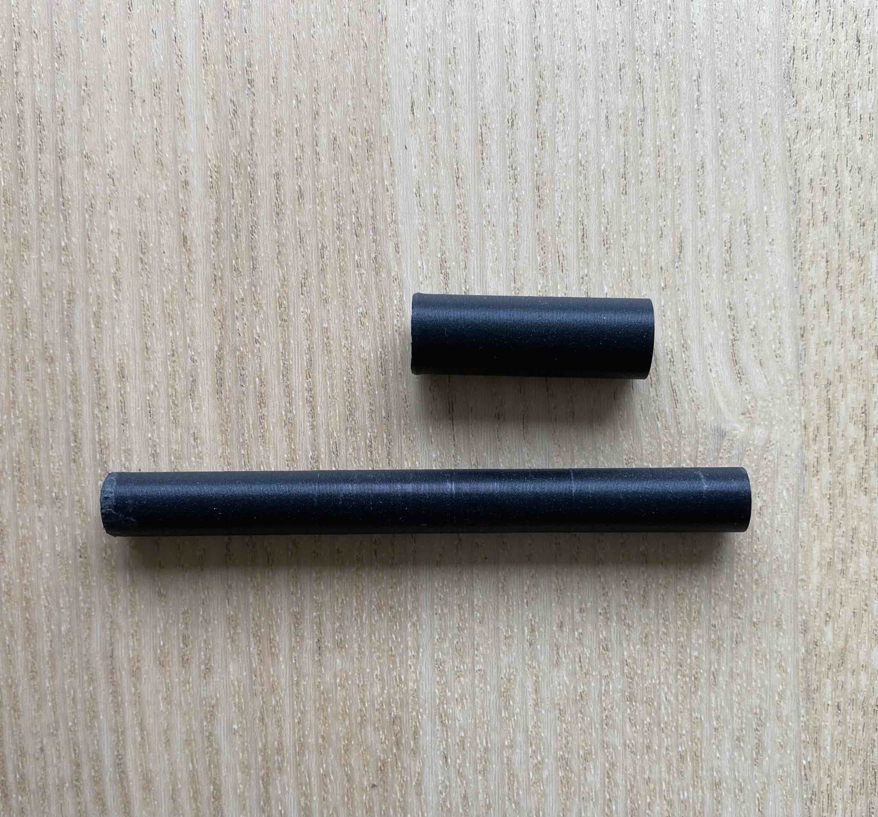
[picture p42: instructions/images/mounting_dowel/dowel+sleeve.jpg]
          
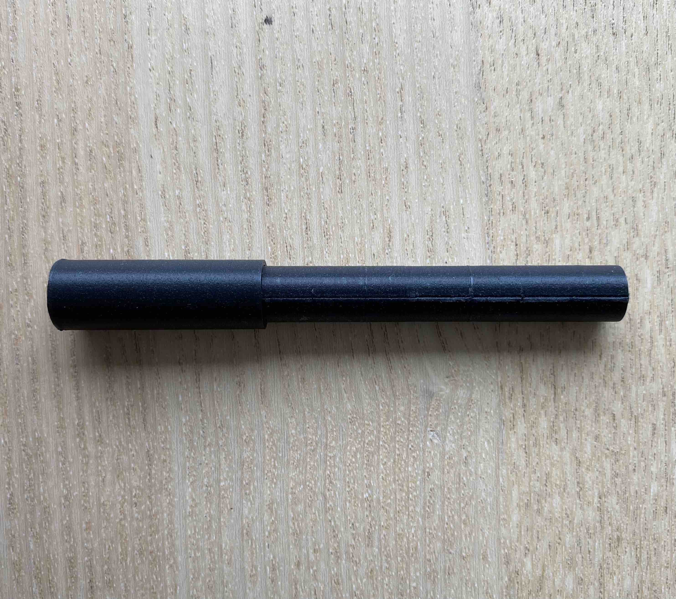
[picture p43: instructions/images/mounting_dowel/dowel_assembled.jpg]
          
    <div>
1. **Read the next step in full before you begin!** 
1. Take your dowel assembly and one ***heat set nut***. Place the nut on the end of the dowel and make sure it's sitting straight. Take your _hot_ soldering iron and hold it against the nut. After a few seconds the nut should beging to melt into the dowel. Try to get it as straight as can be, and make sure the nut's face is flush with the end of the dowel. If it's gone 'too deep,' or crooked, hold your soldering iron against the nut until it is free to move inside the bore and re-adjust as necessary. It does not need to be perfect. Repeat the same step for the other end of the dowel.
     - [Here's a how-to video which shows this process](https://youtu.be/KqSmCHr4fdA?t=165). 
         - Note that this creator uses a special tool, which isn't needed. Any regular soldering tip can do this.
    <div align="center">
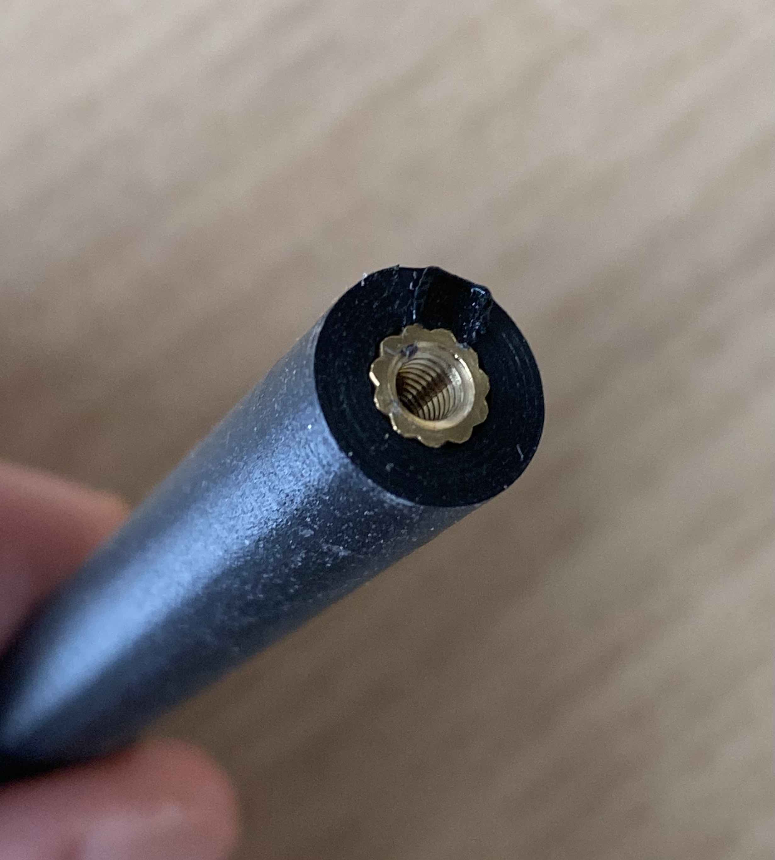
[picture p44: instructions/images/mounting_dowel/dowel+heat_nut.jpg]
        
    </div>
1. Repeat all these steps for each dowel assembly. By the end, you should have 4 completed assemblies.

## Central Support Bearings

### Required parts:
- 2x ***608ZZ Bearings***
- `STRUCT_mid_plate` model
- `STRUCT_back_plate` model

1. Lay the `STRUCT_back_plate` on a flat surface, then lay a ***608ZZ bearing*** overtop of the center housing of each plate.
    <div align="center">
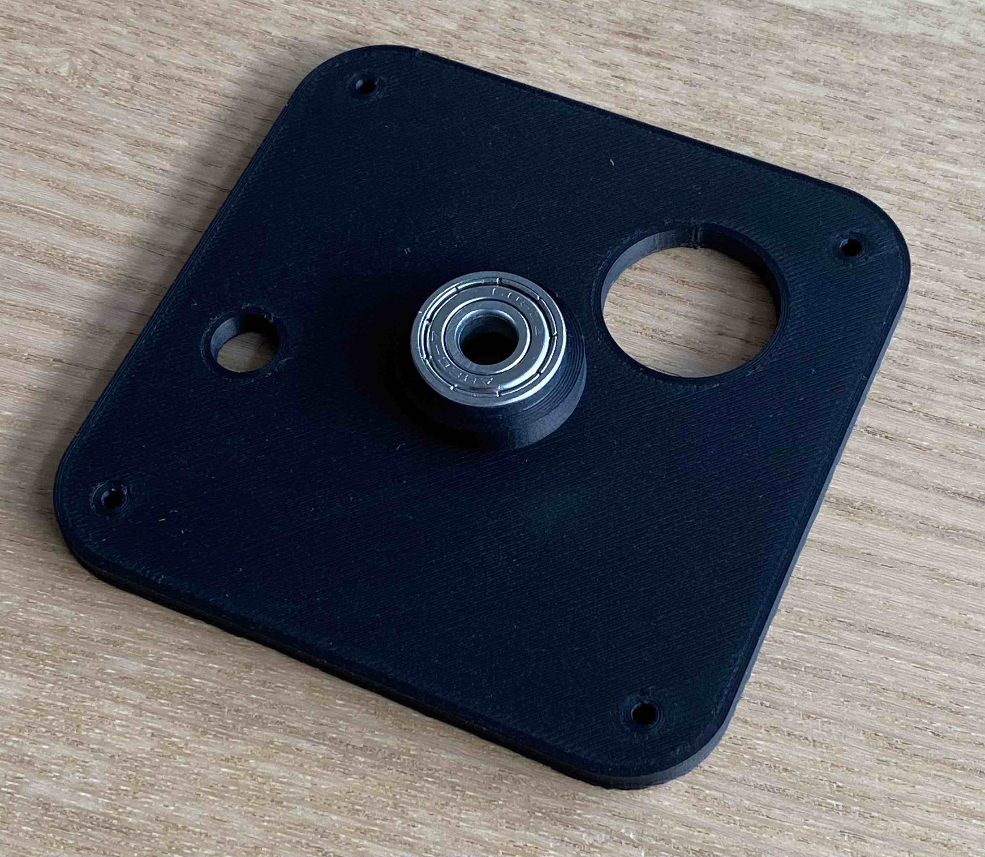
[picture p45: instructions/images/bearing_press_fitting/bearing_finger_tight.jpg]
        
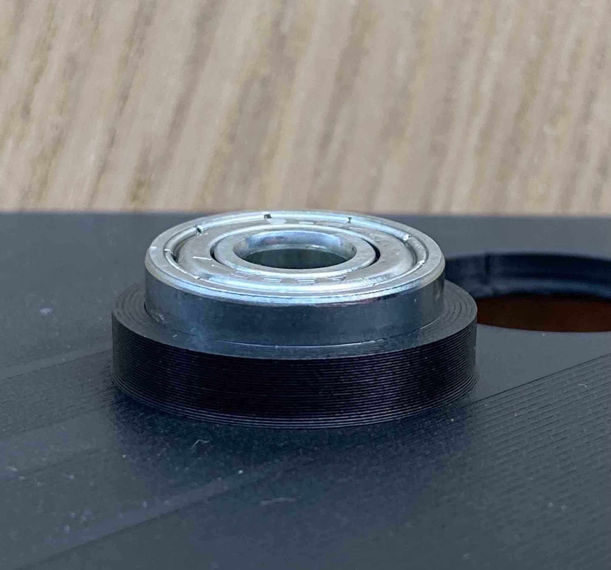
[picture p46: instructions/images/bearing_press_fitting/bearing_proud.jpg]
        
    <div>
1. Gently tap the bearing down until it sits level and flush inside the center housing.
    <div align="center">
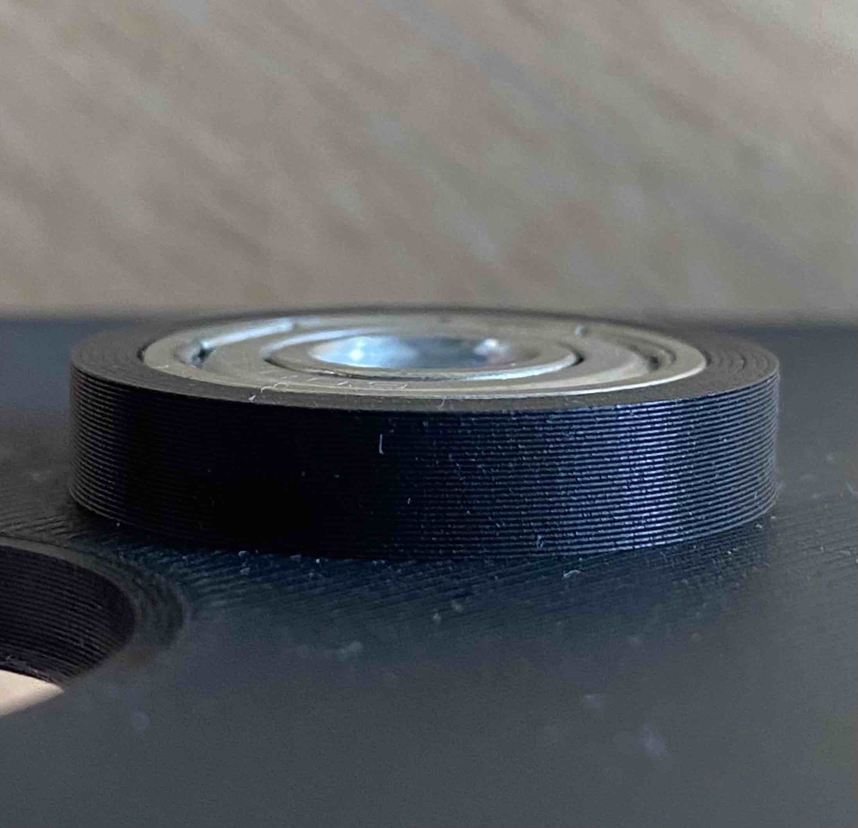
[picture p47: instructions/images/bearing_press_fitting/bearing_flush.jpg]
        
    <div>
1. Repeat the steps above for `STRUCT_mid_plate`

[^1]: https://www.merriam-webster.com/dictionary/bore
[^2]: https://en.wiktionary.org/wiki/flushness#:~:text=(engineering)%20The%20state%20of%20being,smoothly%20aligned%2C%20not%20sticking%20out.

# Final Assembly

### Required parts:
- 4x completed mounting dowel assemblies
- Tensioner assembly
- Watch Jig Assembly
- `clutchless_drive_pulley_v2` model
- Assembled `STRUCT_front_plate`
- Assembled `STRUCT_mid_plate`
- Assembled `STRUCT_back_plate`

1. Get all required parts together and make sure they're complete assemblies; bearings press-fitted, heat nuts secure, sleeves, etc.
    <div align="center">
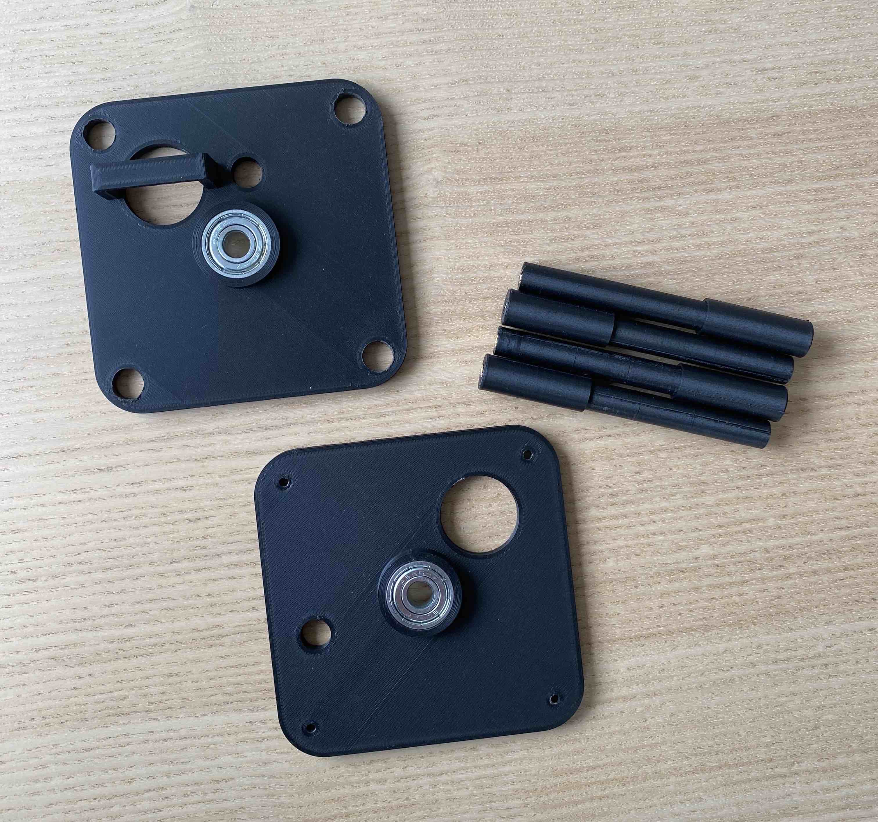
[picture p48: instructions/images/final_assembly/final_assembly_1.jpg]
assembly 1
        
    <div>
1. Begin by inserting the mounting dowel assemblies into the assembled `STRUCT_mid_plate`. Take note of the following numbers
    - **1.** Note the side that the motor housing is on
    - **2.** Note that the thicker end of the mounting dowel assembly faces towards the un-exposed bearing side of the `STRUCT_mid_plate`
        <div align="center">
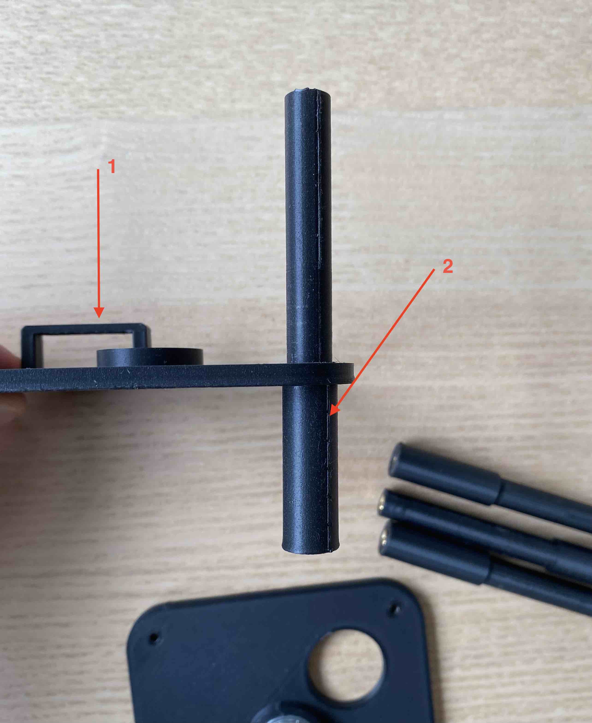
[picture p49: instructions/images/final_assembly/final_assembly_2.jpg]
assembly 2
            
        <div>
1. Insert the remaining mounting dowel assemblies.
        <div align="center">
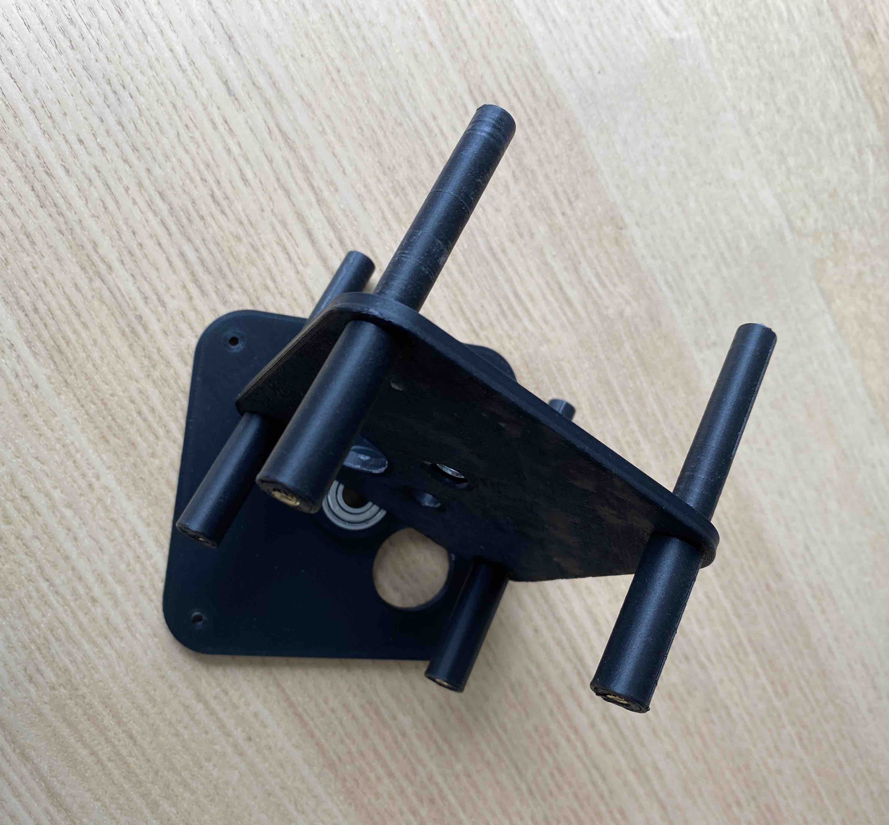
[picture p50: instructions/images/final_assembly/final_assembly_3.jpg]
collection of required parts
            
        <div>
1. Attach the `STRUCT_back_plate`. Make sure to align the motor housing holes.
    - Attach the **Tensioner Assembly** on the lower left hand corner
        <div align="center">
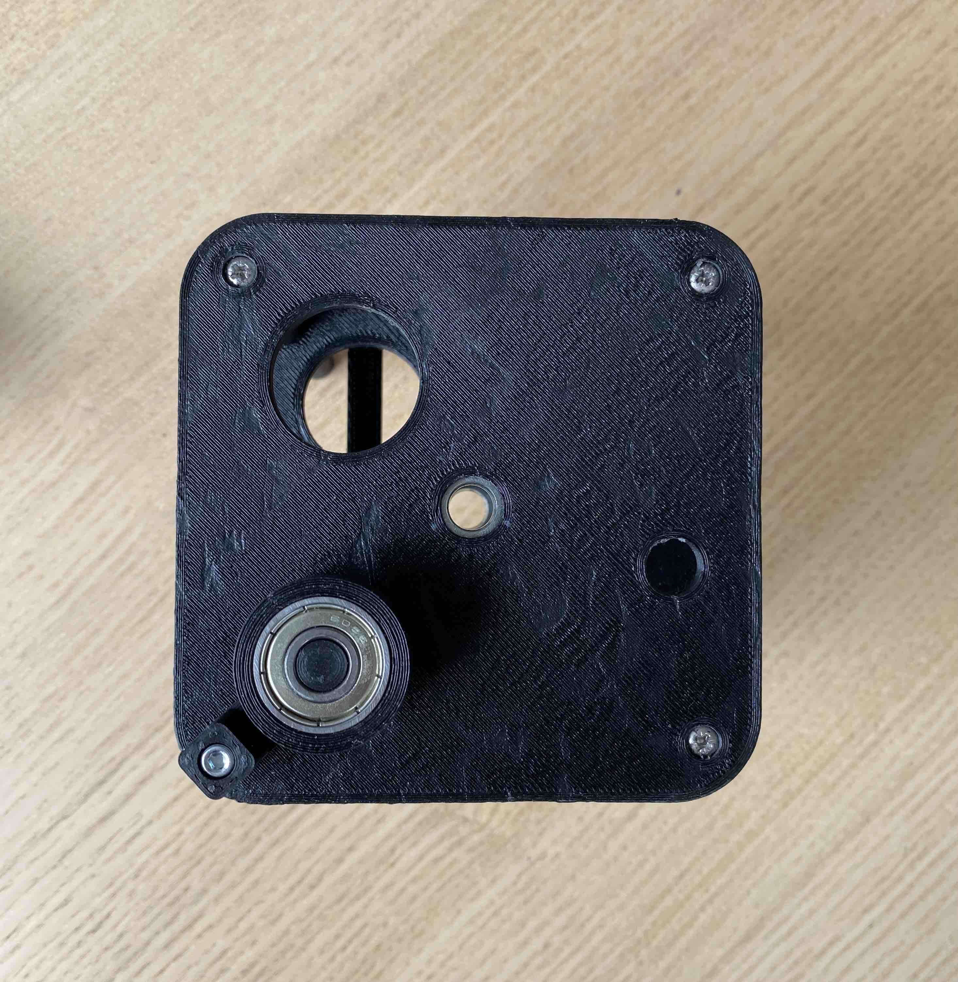
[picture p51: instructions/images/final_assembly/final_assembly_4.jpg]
assembly 3
            
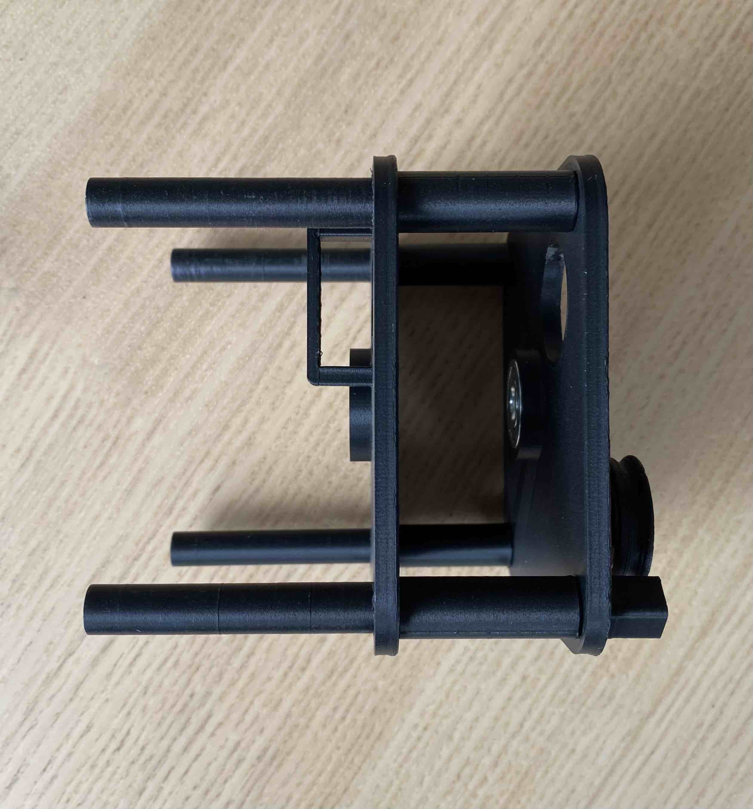
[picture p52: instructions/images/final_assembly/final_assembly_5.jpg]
assembly 4
            
        <div>
1. Attach the `STRUCT_front_plate`.
    <div align="center">
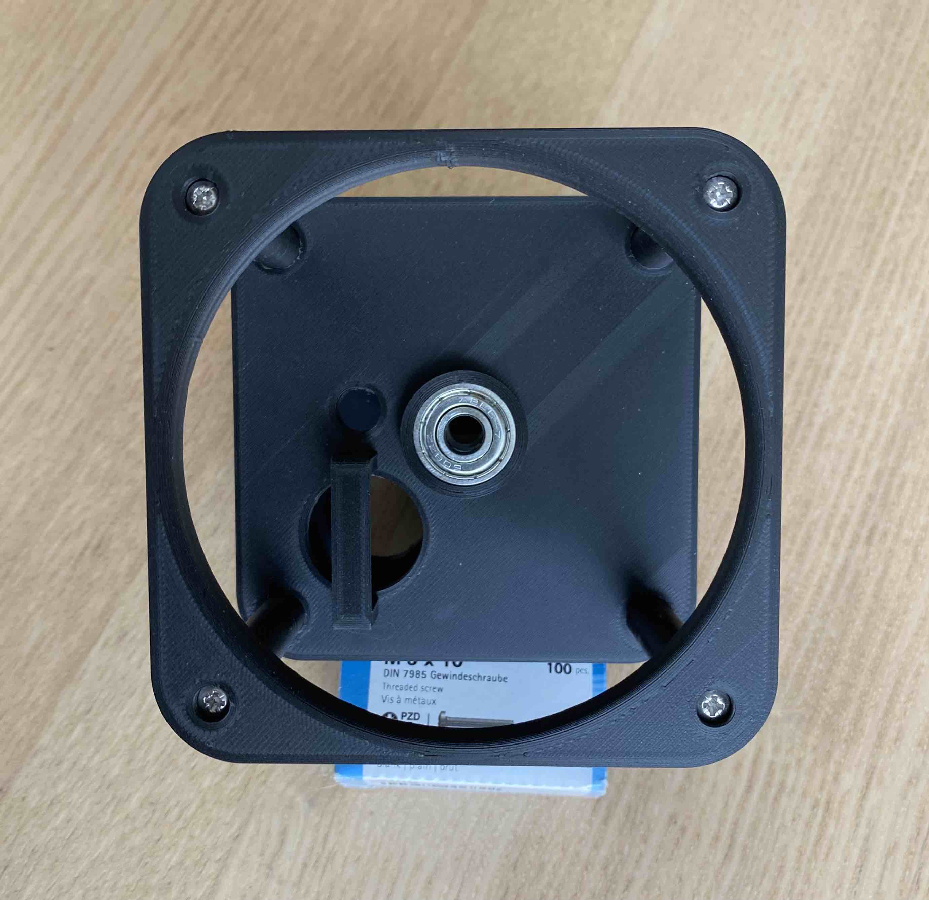
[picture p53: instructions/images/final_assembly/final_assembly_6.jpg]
assembly 6
        
    <div>
1. Apply a small drop of epoxy glue on the watch jig assembly, here:
    <div align="center">
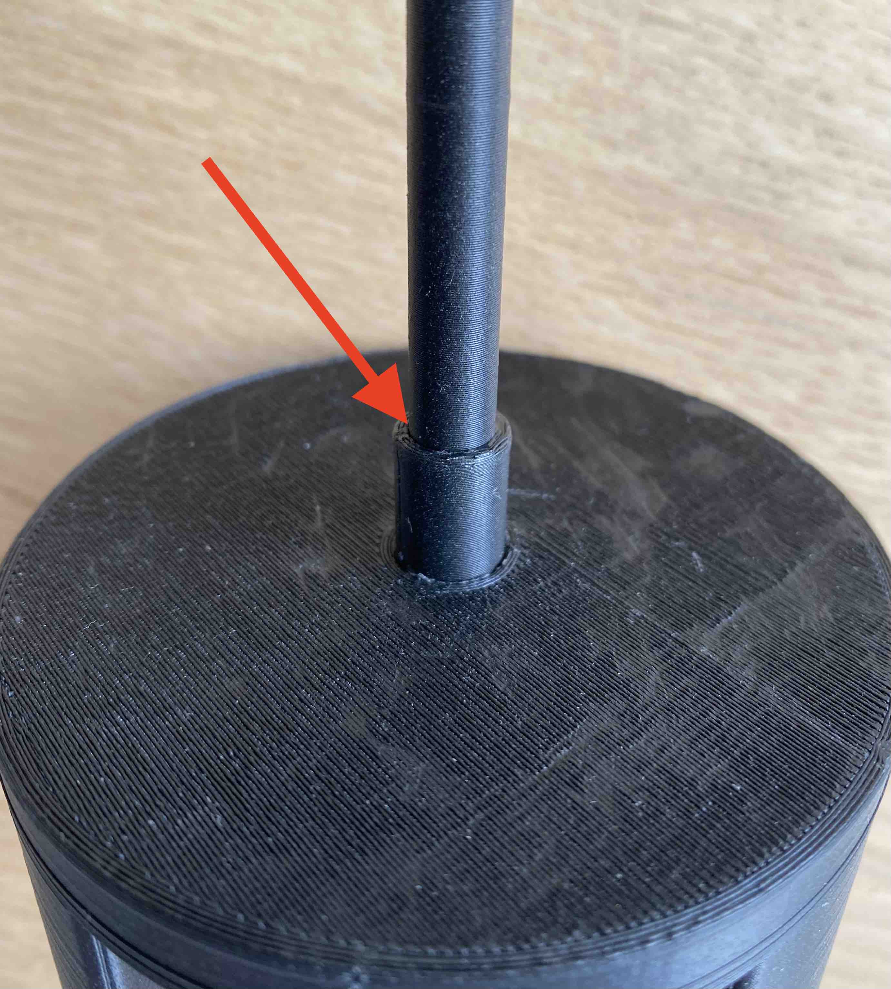
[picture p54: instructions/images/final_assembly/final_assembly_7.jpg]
assembly 7
        
    <div>
1. Begin inserting the watch jig assembly, but before fully seated, add a small drop of epoxy glue, here:
    <div align="center">
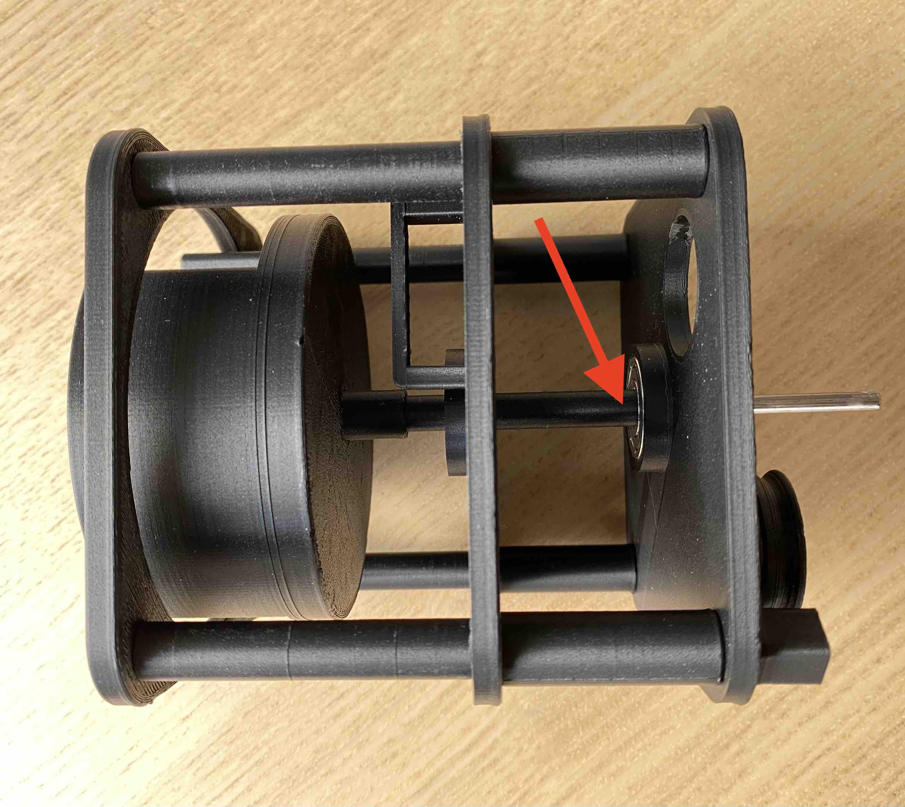
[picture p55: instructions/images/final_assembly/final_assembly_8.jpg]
assembly 8
        
    <div>
1. Fully seat the watch jig assembly and let dry.

1. Decide whether you want to use a clutchless drive pulley, or a clutch drive pulley. You may only build the clutch assembly if you've purchased the optional spring & felt, and printed these optional models:
    - `spring_holder_v3`
    - `top_hat_v2`

    #### Clutchless Drive
    1. After the assembly is dry, slide on the `clutchless_drive_pulley_v2` on the exposed 4mm rod. The model should be a tight fit, but if it isn't, you may attach a hot-melt nut and grub-screw or a fill the hot-melt nut hole with glue. Let dry.
        <div align="center">
            assembly 8
        <div>

    #### Clutch Drive
    1. > Optional: After the assembly is dry, slide an M4 nylon washer down the metal rod. This is optional because you may or may not need it.
    1. Slide the `spring_holder_v3` on to the exposed 4mm rod. The model should be a tight fit but must rotate freely around it's center axis.
    1. Place the spring inside the the `spring_holder_v3`, ensuring the metal rod sits centered within the diameter of the spring; the spring should self center within the `spring_holder_v3`, inside an inner channel. 
    1. Cut a piece of felt the same diameter as the `top_hat_v2` and cut a hole dead center; slide the felt onto the rod and let it sit ontop of the spring. 
    1. Take one hot-melt nut and melt it into the `top_hat_v2`'s horizontal bore. Thread a screw into the hot-melt nut.
        <div align="center">
            top hat hot melt location
        <div>
    1. Slide the `top_hat_v2` down the rod and compress the spring. Tighten the screw in the top hat; it should not rotate on the rod. This will take some trial and error to get the slip-point correct.
    1. Beneath is a reference image to to show the order of each component during assembly. The red disk represents felt.
        <div align="center">
            clutch exploded assembly
        <div>

> If you're building a non-powered winder, you're done! If you're building a powered winder, continue beneath.

### Powered Winder Final Steps

1. Take you motor and solder 2 wires (approx 15cm in length, each) to the contacts on the back of your DC motor.
    <div align="center">
        dc motor with wires attached
    <div>
1. Open the drive belt bag, and attach 2 rubber belts along the length of the body. These will act as shockmounts and make the motor a tight fit. Make sure that the bands "cross" at the front of the motor. If you've done it right, the bands will run parallel down the length of the motor.
    <div align="center">
        motor band back
        motor band front
        motor second band
        motor with parallel bands
    <div>
1. Insert the motor into the large diameter bore, through the back and mid plate.
1. Slide the `motor_drive_pulley_v3` onto the end of the motor
1. [Complete the wiring diagram](./wiring-diagram.md); If you're building a **[Winderoo](https://github.com/mwood77/winderoo)** enabled winder, [see the Winderoo wiring diagram instead](https://github.com/mwood77/winderoo/blob/main/docs/wiring-diagram.md).
1. Insert the completed circuit between mid plate and back plate. You can affix the PCBs and switch using hot glue.
1. Mount a drive belt; loop it around the motor's drive pulley, the central pulley, and the tensioner pulley.
    - If the belt is too loose, try a smaller diameter belt, or swivel the tensioner to tighten the belt.
1. All done!

# Coupling Winders

### Required parts:
- 4x `multi_clip` model
- > Optional: High Position Tensioner Assembly

1. The `multi_clip` model can couple OSWW units together.
1. Attach 4 `multi_clip`s over the thicker diameter portions of the dowel assemblies of each OSWW unit - you should have 2 clips on top, and 2 on the bottom.
1. Couple the pulleys of the secondary OSWW to the first OSWW using a spare drive belt. If you need to adjust the tension, swap the tensioner assembly to a High Position Tensioner Assembly

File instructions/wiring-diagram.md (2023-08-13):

> [👈 Back to main page](../README.md)

# Wiring Diagram - OSWW
fritzing wiring diagram

<div align="center">
    <a href="./images/osww.pdf">Is the image hard to view? Open the PDF instead</a>
</div>
<br />

- Connect the Pi Pico's `VBUS` pin to the 5V input of the L298N driver board (red wire)
- Connect a ground from the Pi Pico the L298N driver board (black wire)
- Connect the L298N driver board's 5V and 12V terminals together (red jumper wire)
- Make sure the L298N's jumpers are in place (small blue wires on board)
- Connect the Pi Pico's `GPIO10` to `IN1` on the L298N driver board (yellow wire)
- Connect the Pi Pico's `GPIO11` to `IN2` on the L298N driver board (blue wire)
- Connect the DC motor to channel 1 on the L298N driver board.
    - > Note: polarity does not matter here
    - You may add a in-line switch between the motor and the L298N driver board; this will enable and disable winding

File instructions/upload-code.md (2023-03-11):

# Uploading the Code

### Have you completed the Prerequisites?
- [No? Find them in the README](../README.md#prerequisites)

## Flashing your microcontroller

1. Connect your Pi Pico
1. Open the `osww.ino` file in the Arduino IDE
1. Ensure the project compiles first; click on **Sketch > Verify/Compile**
    - If you see the following, all is OK:
        ```
        Sketch uses 90822 bytes (4%) of program storage space. Maximum is 2097152 bytes.
        Global variables use 42888 bytes (15%) of dynamic memory, leaving 227448 bytes for local variables. Maximum is 270336 bytes.
        ```
1. Upload the code; **Sketch > Upload**
    - If you see the following, all is OK:
        ```
        Sketch uses 90822 bytes (4%) of program storage space. Maximum is 2097152 bytes.
        Global variables use 42888 bytes (15%) of dynamic memory, leaving 227448 bytes for local variables. Maximum is 270336 bytes.
        .
        ```
1. All done!

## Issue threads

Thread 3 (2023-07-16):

Provide model files

kjsmita6, 2023-07-16:
Hello, is it possible to provide the model files (SLDPRT, DWG, etc) so people can modify them? For example, the provided watch mount only fits one of my automatic watches. It would be great to be able to modify this to be able to hold more. I don't think the STL can really be modified in such a way (besides scaling) so having these files would be best.

kjsmita6, 2023-07-16:
Nevermind, within 1 minute of opening this issue I saw that there are source files already.

Closed 2023-07-16.

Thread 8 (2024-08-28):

BOM item "Electric Motor with gear reduction" link does not work.

erimsa, 2024-08-28:
BOM item "Electric Motor with gear reduction" link is removed from Aliexpress.

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

mwood77, 2024-08-29:
BOM updated: https://github.com/mwood77/osww/commit/890974d3d81d2fde0b7f9a80a5ce03aaf5c2bfa3

erimsa, 2024-08-29:
Thanks.

Closed 2024-08-29.

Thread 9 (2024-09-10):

Why are mounting_dowel and mounting_dowel_sleeve two separate files ?

azsde, 2024-09-10:
Hi

I am wondering why those are two separate files that needs to be pressed together ?

Isn't it simpler to just "merge them" and have a cylinder with a bigger diameter on one part and a smaller diameter on the rest of the part ?

mwood77, 2024-09-12:
Hi,

These pieces were created separately as press-fit, because I cannot guarantee the tolerances of all printers. These pieces interact not only with themselves, but also a metal rod, and a bearing's inner-race. So there's the potential of a lot going wrong.

If they were merged into a single print, the chances of failure are much higher. For example, if the bottom of the larger print delaminates from the print bed, the mounting hole could become warped and the print has to be re-done. That's a bummer as it's a 3+ hour print.

Separating the pieces into a larger print + a smaller high-tolerance print means that, should the tolerance(s) need to be adjusted for your situation, it's a re-size of a basic cylinder and a printing time of 5 minutes.

Closed 2024-10-08.

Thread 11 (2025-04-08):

More models require support

knmorgan, 2025-04-08:
The [printing recommendations](https://github.com/mwood77/osww/blob/main/instructions/printing-recommendations.md) make the following suggestion.

> The following models will require support:
> * STRUCT_mid_plate
> * watch_mount

However, after failing to print a large batch of parts, I noticed three other files clearly need supports as well. Specifically, `clutchless_drive_pulley_v2`, `motor_drive_pulley_v3`, and `spring_holder_v3` all have overhanging sections that are impossible to bridge and are likely to cause a print to fail.

mwood77, 2025-04-08:
What is your printer and print settings?

I printed everything on an Ender 3 V2 without supports, except for the following models `STRUCT_mid_plate` and `watch_mount`.

---

There is a user submitted print profile for bambu machines here: https://makerworld.com/en/models/978704-osww-the-open-source-watch-winder#profileId-1190285

knmorgan, 2025-04-08:
The print profile that you linked contains supports for the three objects I mentioned.

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

The printer and print settings aren't particularly relevant here. If you observe the geometry of these three parts they all require overhang perimeters, which are impossible to print cleanly on an FDM printer.

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

mwood77, 2025-04-09:
Nice, feel free to update the docs and open a PR.

Closed 2025-04-21.

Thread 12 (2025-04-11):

Nut & screw dimensions for clutch drive variant (top_hat_v2)

richiehug, 2025-04-11:
In the build guide under the [Clutch Drive](https://github.com/mwood77/osww/blob/main/instructions/build-guide.md#clutch-drive) section, the instructions says the following;

> take one hot-melt nut and melt it into the `top_hat_v2`'s horizontal bore and then thread a screw into it.

I noticed that the bore for the hot-melt nut is smaller than the one used in the Mounting Dowel Assembly (`mounting_dowel_v3`). I used a slightly smaller M3 nut (4.2mm wide, 3mm tall), but this barely fits into the `top_hat_v2`'s horizontal bore. Could you please specify the intended nut's dimensions to ensure a proper fit? Clarifying this in the documentation would help avoid assembly issues for others.

Here's an image of my `top_hat_v2` using the nut specified above:

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

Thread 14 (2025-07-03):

Arduino-based mods

tomotvos, 2025-07-03:
I have been working on an Arduino-based variant of OSWW, and your Fusion file helped immensely. The question is: how best to contribute those changes back? Do you want a separate branch for this, or a PR with a new Fusion file and STLs? The way you have your components versioned in Fusion, I am not sure I can easily create distinct versions of components, but maybe there is a way.

Major changes include the back plate for mounting an Arduino stepper motor, and different pulleys.

The source file for the .ino is the easiest mod to contribute.

Of course, I can fork everything but this is such a great project that it would be a shame to not have everything in one place.

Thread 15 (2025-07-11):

Missing BOM for grub screws

orogvany, 2025-07-11:
Looks like the bom is missing the grub screws.

Also, i did notice that the BOM heatserts were not a great fit for the rods, the diameter hole for the rods should be a bit tighter, though maybe the supplied link for parts changed what they send.  can take measurements if you'd like what I'm seeing here.

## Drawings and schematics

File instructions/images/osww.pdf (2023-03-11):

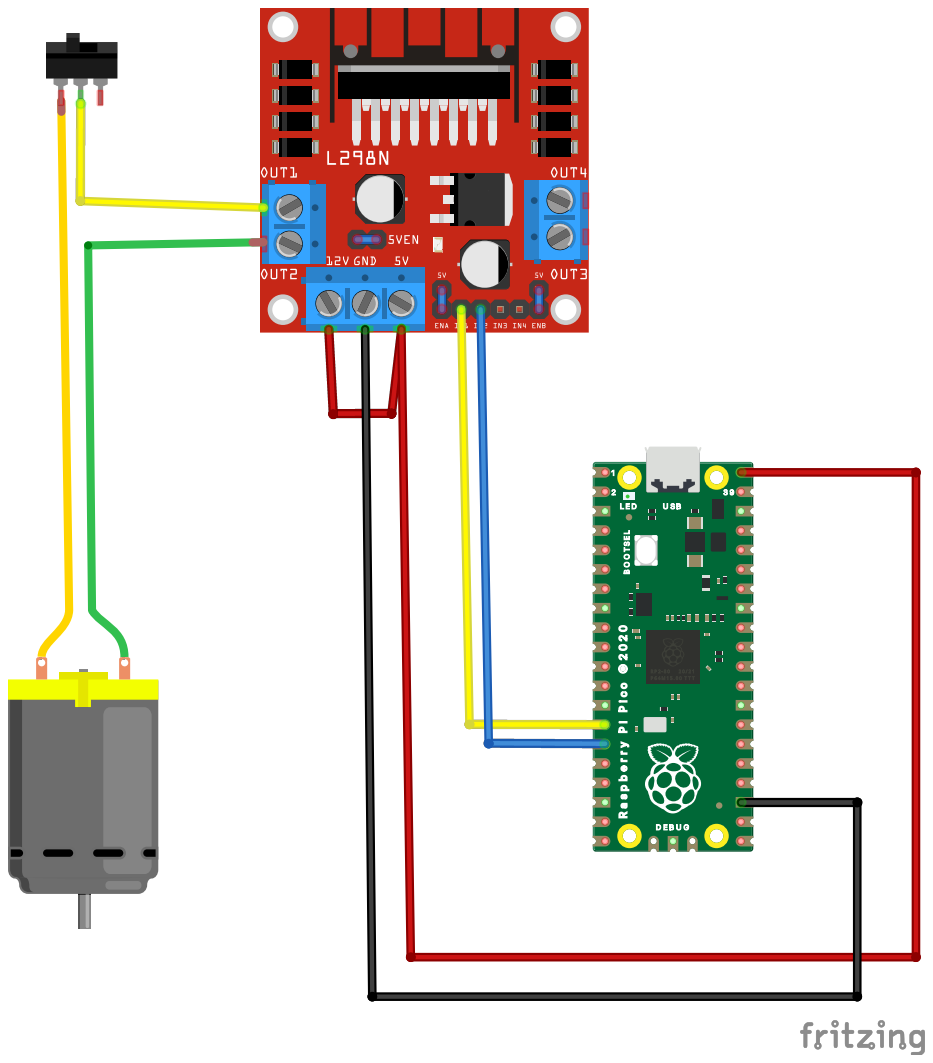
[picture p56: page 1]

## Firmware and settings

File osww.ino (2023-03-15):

#include "MotorControl.h"

/*
 * *************************************************************************************
 * ********************************* CONFIGURABLES *************************************
 * *************************************************************************************
 *
 * If you purchased the motor listed in the guide / Bill Of Materials, then this default value is correct!
 * 
 * directionalPinA = this is the pin that's wired to IN1 on your L298N circuit board
 * directionalPinB = this is the pin that's wired to IN2 on your L298N circuit board
 * externalButton = OPTIONAL - If you want to use an external momentary button to pause operation, connect it to this pin along with a resistor to ground. If you need to use another pin, change the value here.
 */
int directionalPinA = 10;   // GPIO 10
int directionalPinB = 11;   // GPIO 11
int externalButton = 14;    // GPIO 14

// direction can be:
//      "BOTH"
//      "CW"    <-- Clockwise
//      "CCW"   <-- Counter Clockwise
//
// -- If you want your winder to turn clockwise only, replace the direction value with "CW"
// -- If you want your winder to turn counter clockwise only, replace the direction value with "CCW"
// -- If you want your winder to turn both directions, replace the direction value with "BOTH"
//
// timeToRotateInSeconds = this is how long the motor will rotate for without stopping. Default is 180 seconds (3 minutes)
// timeToPauseInSeconds = this is how long the pause duration will be during motor operation. Default is 3 seconds
struct RUNTIME_VARS
{
  String direction = "BOTH";
  bool routineRunning = false;
  int timeToRotateInSeconds = 180;
  int timeToPauseInSeconds = 3;
};
/*
 * *************************************************************************************
 * ******************************* END CONFIGURABLES ***********************************
 * *************************************************************************************
 */

/*
 * DO NOT CHANGE THESE VARIABLES!
 */
int currentSeconds = 0;
RUNTIME_VARS userDefinedSettings;
MotorControl motor(directionalPinA, directionalPinB);

/**
 * Sets running conditions to TRUE & calculates winding time parameters
 */
void beginWindingRoutine()
{
  userDefinedSettings.routineRunning = true;

  if ((strcmp(userDefinedSettings.direction.c_str(), "CW") == 0)) 
  {
    motor.setMotorDirection(1);
  }

  Serial.println("[STATUS] - Begin winding routine");
}

void setup()
{
  Serial.begin(9600);
  delay(5000);

  // Prepare pins
  pinMode(directionalPinA, OUTPUT);
  pinMode(directionalPinB, OUTPUT);
  pinMode(externalButton, INPUT);

  beginWindingRoutine();
  motor.determineMotorDirectionAndBegin();
}

void awaitWhileListening(int pauseInSeconds)
{
  // While waiting for the 1 second to pass, actively monitor/listen for button press.
  int delayEnd = millis() + (1000 * pauseInSeconds);
  while (millis() < delayEnd) {
    // get physical button state
    int buttonState = digitalRead(externalButton);

    if (buttonState == HIGH) {
      Serial.println("[STATUS] - Button pressed");
      userDefinedSettings.routineRunning = !userDefinedSettings.routineRunning;
    }
  }
}

void loop()
{
  if (userDefinedSettings.routineRunning)
  {
    if (currentSeconds >= userDefinedSettings.timeToRotateInSeconds)
    {
      currentSeconds = 0;
      motor.stop();
      awaitWhileListening(userDefinedSettings.timeToPauseInSeconds);
      if (strcmp(userDefinedSettings.direction.c_str(), "BOTH") == 0)
      {
        int currentDirection = motor.getMotorDirection();
        motor.setMotorDirection(!currentDirection);
        Serial.println("[STATUS] - Motor Pause - mode is BOTH");
      }
      motor.determineMotorDirectionAndBegin();
    }
  } else {
    motor.stop();
  }
  awaitWhileListening(1);
  currentSeconds++;
}

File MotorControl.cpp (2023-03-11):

#include "MotorControl.h"

MotorControl::MotorControl(int pinA, int pinB)
{
    _pinA = pinA;
    _pinB = pinB;
    _motorDirection = 0;
}

void MotorControl::clockwise()
{
    digitalWrite(_pinA, HIGH);
    digitalWrite(_pinB, LOW);
    Serial.println("[STATUS] - Motor turning clockwise");
}

void MotorControl::countClockwise()
{
    digitalWrite(_pinA, LOW);
    digitalWrite(_pinB, HIGH);
    Serial.println("[STATUS] - Motor turning counter clockwise");
}

void MotorControl::stop()
{
    digitalWrite(_pinA, LOW);
    digitalWrite(_pinB, LOW);
}

void MotorControl::determineMotorDirectionAndBegin()
{
    stop();

    if (_motorDirection)
    {
        clockwise();
    }
    else
    {
        countClockwise();
    }
}

int MotorControl::getMotorDirection()
{
    return _motorDirection;
}

void MotorControl::setMotorDirection(int direction)
{
    _motorDirection = direction;
}

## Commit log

2023-03-11 add wiring diagram
    [osww.fzz]
2023-03-11 add final assembly steps
2023-03-14 - Update BOM with motor specifics - Add models for clutch assembly - Update documentation - Parameterize rotation and pause duration - Add support for pause via external momentary button
    [spring_holder_v3.stl, top_hat_v2.stl]
2023-03-15 Bug Fix: Missed Button Press - Cleanup Logic (#1)
    * Cleanup loop logic and fix missed button presses
    Cleans up the loop logic, as well as fixes the bug of missing button presses due to using the delay function.
    * change to millis() for Arduino support
    Changing to millis() function for arduino support.
    [osww.ino]
2023-04-01 Add cad source files (#2)
    * add cad source files
    * add cad source files
    [osww-v39-april-1-2023.f3d, osww-v39-april-1-2023.step]
2023-08-13 update BOM broken link and add winderoo links for wiring diagram
2024-05-04 add callout for winderoo esp32 (#6)
2024-08-29 update bom with new motor link
2024-10-09 Fix broken links in BOM & remove affiliate links (#10)
    * fix broken links in BOM & remove affiliate links
    * typos
2026-05-18 update BOM for #16 (#18)
